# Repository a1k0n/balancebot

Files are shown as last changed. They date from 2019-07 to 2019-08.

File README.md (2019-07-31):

# balancebot
Small DC-motor based balancing robot.

picture of bot standing upright

BalanceBot video (http://www.youtube.com/watch?v=YxdkzbH74xc "BalanceBot in motion")

Parts:
 - 130-size DC motor (w/ capacitors soldered between wires and case -- this prevents catastrophic amounts of noise on the power supply rail!)
 - Digispark
 - Digispark motor shield
 - Adaboost LiPo battery charger
 - LiPo battery
 - MPU-9250 accelerometer/gyro/compass (compass not used, MPU-6050 would also work)
 - 3D printed frame, wheels+axle+spur gear, pinion gear
 - rubber bands for tires
 - M2.5 screws for the PCBs and servo tape to hold on the battery / power switch

3d parts

This is all stuff I had on hand; if I were to design it around parts which can be bought new, I would do
it differently. There are better/cheaper microcontroller boards w/ integrated charging, ARM CPU, more IO for example.

It does not have any sort of wheel encoder, which means it doesn't know where its own CG is, or how far from the
center position it has travelled. It tries to guess this by summing up all motor outputs over time, and adds this
as a small bias to the desired upright angle which causes it to gently roll back and forth which doubles as a "demo".
The CG bias is just hardcoded; if I move the battery it'll have to be adjusted manually.

There are still issues with the I2C bus glitching from the motor's activity which causes the Arduino Wire
library to get stuck in an infinite loop. I would use SPI instead of I2C for the MPU-9250 except the motor
shield is using the MOSI pin.

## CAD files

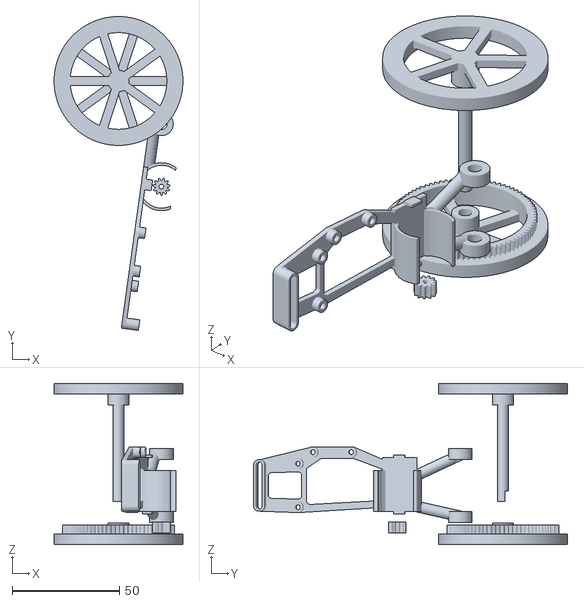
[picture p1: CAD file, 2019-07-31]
allparts.stl
60.0 x 146.1 x 75.0

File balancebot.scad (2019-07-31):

$fs = 0.1;

use <pd-gears.scad>;

// explode assembly apart for 3d printing preparation
apart = 20;

pitch = 2;
n1 = 11;
n2 = 80;


motor_axle_spacing = pitch_radius(pitch, n1) + pitch_radius(pitch, n2) + 0.25;

module wheel() {
  union() {
    difference() {
      cylinder(h=5, d=60, $fn=100);
      translate([0, 0, -0.1]) cylinder(h=5.2, d=45, $fn=100);
    }
    cylinder(h=10, d=10);
    for (i = [0:5]) {
      rotate([0, 0, i*360/5]) translate([0, -2, 0]) cube([25, 4, 3]);
    }
  }
}

buildthick = 2;
buildplane_ang = acos((7.5 + buildthick - 5.5) / motor_axle_spacing);

module motormount() {
  wall = 1.2;  // 3x nozzle
  translate([0, 0, 10])
    difference() {
      cylinder(h=19, d=20+2*wall);
      translate([0, 0, -0.1]) cylinder(h=19.2, d=20);
      translate([-11, -7.5-8, -0.1]) cube([22, 10, 19.2]);
      translate([-11, 7.5, -0.1]) cube([22, 10, 19.2]);
    }
  translate([-2.5, 7.5-3, 10-wall]) cube([5, 4, wall]);
  translate([-8, 7.5, 10]) cube([16, buildthick, 25]);
  translate([-2.5, 7.5-3, 35]) cube([5, 4, wall]);
}

module pcbmounts(tail) {
  offset = 3+buildthick;
  d = 5;
  screw_drill = 2.5;

  %translate([0, -36/2, offset]) cube([23, 36, 1]);
  %translate([25, -26/2, offset]) cube([15.5, 26, 1]);
  %translate([44, -19/2, 0]) cube([17, 19, 1]);
  %translate([44, -12.3/2, 0]) cube([27, 12.3, 1]);
  %translate([44, -18/2, 0]) cube([2.54, 15.77, 9]);

  mountpts = [
    [2.5, -36/2+2.5],
    [23-2.5, -36/2+2.5],
    [25+2.5, 20.25/2],
    [25+2.5, -20.25/2],
  ];
  difference() {
    union() {
      linear_extrude(buildthick) hull() {
        for (m = mountpts) {
          translate(m) circle(d=d);
        }
        translate(tail) circle(d=20);
        translate([44+2.54/2, -19/2, 0]) circle(d=5);
        translate([44+2.54/2, 19/2, 0]) circle(d=5);
      }
      for (m = mountpts) {
        translate(m) cylinder(d=d, h=offset);
      }
      linear_extrude(8) hull() {
        translate([44+2.54/2, -19/2, 0]) circle(d=5);
        translate([44+2.54/2, 19/2, 0]) circle(d=5);
      }
    }
    for (m = mountpts) {
      translate([m[0], m[1], -0.1]) cylinder(d=screw_drill, h=offset*2);
    }
    linear_extrude(9) hull() {
      translate([44+2.54/2, -19/2, 0-0.1]) circle(d=3);
      translate([44+2.54/2, 19/2, 0-0.1]) circle(d=3);
    }
    scale([0.8, 0.7, 1.5]) translate([0,0,-0.1]) linear_extrude(buildthick) hull() {
      for (m = mountpts) {
        translate(m) circle(d=d);
      }
      translate(tail) circle(d=20);
    }
    translate([26, 0, 0]) scale([0.7, 0.5, 1.5]) translate([0,0,-0.1]) linear_extrude(buildthick) hull() {
      translate([2.5, 20.25/2]) circle(d=d);
      translate([2.5, -20.25/2]) circle(d=d);
      translate([44+2.54/2-25, -19/2, 0]) circle(d=5);
      translate([44+2.54/2-25, 19/2, 0]) circle(d=5);
    }
  }
}

union() {
  translate([apart, 0, 5.5]) {
    rotate([0, 0, buildplane_ang]) {
      motormount();
    }
    rotate([0, 0, 180/n1]) gear(pitch, n1, 5, 2.2, twist=0);
  }
  translate([apart, 0, 0]) rotate([0, 0, buildplane_ang-90]) rotate([-90, 0, 0]) rotate([0, 90, 0]) {
    translate([20, -55/2, -7.5-buildthick]) pcbmounts([-15, 0, 0]);
  }

  translate([0, motor_axle_spacing + apart, 5]) {
    gear(pitch, n2, 4, 45, twist=0, $fn=100);
    translate([0, 0, -5]) difference() {
      wheel();
      difference() {
        cylinder(h=10.1, d=5.1);
        translate([-2.5, 1, 0]) cube([5, 5, 5]);
      }
    }
  }

  translate([0, motor_axle_spacing + apart, 55 + apart]) rotate([0, 180, 0]) {
    wheel();
    difference() {
      cylinder(h=55, d=5.0);
      translate([-2.5, 1, 50]) cube([5, 5, 5]);
    }
  }


  // beam connecting motor to axle, wheel hubs
  r=2.5;
  y0 = 7.5 + buildthick - r;
  difference() {
    union() {
      hull() {
        translate([apart, 0, 0]) rotate([0, 0, buildplane_ang]) {
          translate([0, y0, 55/2 - 8]) sphere(r=r);
          translate([motor_axle_spacing, y0, 10.5+2.5]) sphere(r=r);
        }
      }
      hull() {
        translate([apart, 0, 0]) rotate([0, 0, buildplane_ang]) {
          translate([0, y0, 55/2 + 1]) sphere(r=r);
          translate([motor_axle_spacing, y0, 55-10.5-2.5]) sphere(r=r);
        }
      }
      translate([apart, motor_axle_spacing, 10.3]) cylinder(h=5, d=11);
      translate([apart, motor_axle_spacing, 55-10.3-5]) cylinder(h=5, d=11);
    }
    translate([apart, 0, 0]) cylinder(h=100, d=20+2*1.2-0.1);
    translate([apart, motor_axle_spacing, 0]) cylinder(h=100, d=5.3);
  }
}

*pcbmounts([-15,0,0]);

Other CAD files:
pd-gears.scad

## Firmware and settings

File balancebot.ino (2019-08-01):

#include <Wire.h>

static const int MotorDir = 5;
static const int MotorSpeed = 1;

uint8_t i2caddr = 0x68;

const uint8_t PROGMEM mpu9250conf[] = {
  107, 0,
  107, 1,
  108, 0,
  55, 0x32,  // bypass_en for magnetometer
  25, 0x00,  // samplerate divisor = 0
  26, 0x00,  // dlpf_cfg = 0
  27, 0x10,  // gyro_conf: gyro_fs_sel = 1000dps
  28, 0x00,  // +-2g full scale
  29, 0x05,  // accel dlpf = 0 (218Hz BW)
};

void setup() {
  // put your setup code here, to run once:
  pinMode(MotorDir, OUTPUT);   
  pinMode(MotorSpeed, OUTPUT);
  Wire.begin();

  // hold MPU-9150 in reset for 10ms
  Wire.beginTransmission(i2caddr);
  Wire.write(107);
  Wire.write(0x80);
  Wire.endTransmission();
  delay(10);

  for (uint8_t i = 0; i < sizeof(mpu9250conf); i += 2) {
    Wire.beginTransmission(i2caddr);
    Wire.write(pgm_read_byte(mpu9250conf+i));
    Wire.write(pgm_read_byte(mpu9250conf+i+1));
    Wire.endTransmission();
  }
  
  //DigiUSB.begin();
  //DigiUSB.println(F("starting up!"));
}

int16_t readreg16(uint8_t addr) {
  Wire.beginTransmission(i2caddr);
  Wire.write(addr);
  if (Wire.endTransmission(false) != 0) {
    return 0;
  }
  if (Wire.requestFrom(i2caddr, 2) != 0) {
    // reset the bus?
    Wire.begin();
    return 0;
  }
  int16_t res;
  res = Wire.read() << 8;
  if (!Wire.available()) return 0;
  res += Wire.read();
  while (Wire.available()) {
    Wire.read();
  }
  return res;
}

int16_t readgy() {
  return readreg16(0x45);
}

int16_t readaz() {
  return readreg16(0x3f);
}

void loop() {
  // use complementary filter to compute angle
  int32_t angle = 0;
  int32_t xsum = 0;
  int32_t u = 0, dxsum = 0;
  uint16_t n_ = 0;
  for (;;) {
    unsigned long t0 = millis();
    int16_t az = readaz();  // +- full scale of 2g; 16384 = 1g
    int16_t gy = readgy();  // 1000dps full scale; 32768 = 1000 deg/s = ~17.45 rad/s

    // az = 1g * sin(theta) = 16384 * sin(theta)
    // gy = dtheta/dt * 1877.4681030846816
    // dt = 0.01s (100Hz main loop)
    
    angle += gy;  // angle = 187746.81030846816 * theta (rad)
    angle -= angle >> 4;  // leaky integrator (high pass filtered, tau=0.15s)
    angle -= az >> 1;  // ~ 2048*theta (radians), low-pass filtered az (ideally, 2933*theta)

    // don't attempt to drive if we're already tipped over
    if (angle > -74000 && angle < 74000) {
      int32_t anglecg = 9000 - (xsum<<2) + (dxsum << 4);
      u = ((angle - anglecg) >> 5) + (gy >> 5);
      if (u > 255) u = 255;
      if (u < -255) u = -255;

      dxsum = u - (xsum >> 7);
      xsum += dxsum;
      
      uint16_t sp = (u < 0 ? -u : u);
      digitalWrite(MotorDir, u<0 ? 0 : 1);
      analogWrite(MotorSpeed, sp);
    } else {
      analogWrite(MotorSpeed, 0);
      xsum = 0;
    }

    // program loop 100Hz
    while (millis() - t0 < 10) {
      //DigiUSB.refresh();
    }
  }
}

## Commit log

2019-07-31 code + model for balancing robot
    [allparts.stl, balancebot.scad, pd-gears.scad]
2019-08-01 tightened up the motion around the centerpoint
    it rocks back and forth a bit faster without being too jerky
    [balancebot.ino]
